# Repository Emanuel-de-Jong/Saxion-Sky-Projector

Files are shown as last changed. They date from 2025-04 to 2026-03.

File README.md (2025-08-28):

# Sky Projector
For the class: 3.3 CDT Increadible machines

A DIY controllable and customizable 3-in-1 sky projector. The code is nothing special, but the technical components, prototyping and planning were interesting. I made a schematic and a 3d model and used components like MOSFETs and PWM Drivers.

With the high power LEDS, I also had to take heat into account in multiple places. Aluminium bases, a fan and even a thick heatsink were needed.

**Active Development:** 2025-03-17 - 2025-04-21<br>
**Last Change:** 2025-05-08<br>

| | |
| :---: | :---: |
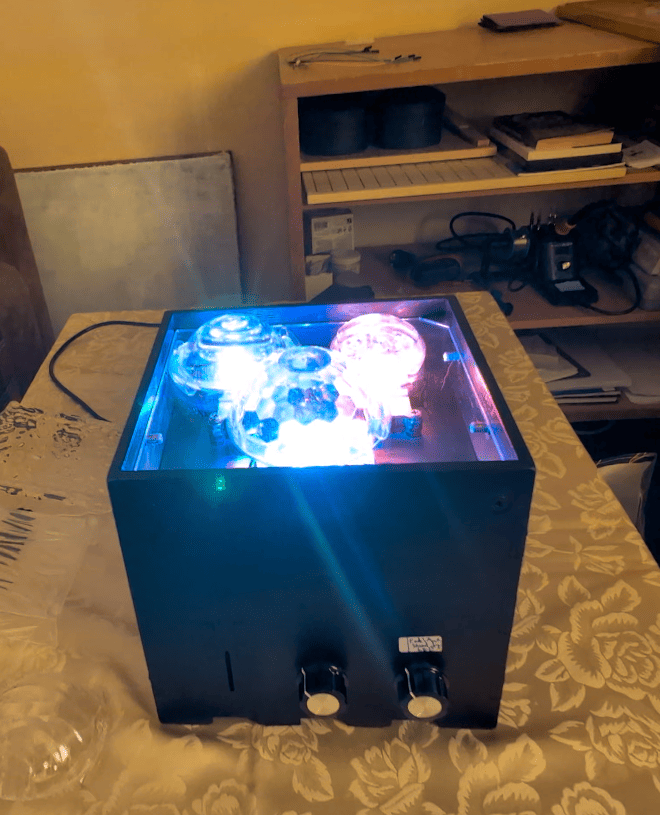
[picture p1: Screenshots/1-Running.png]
|  |  |
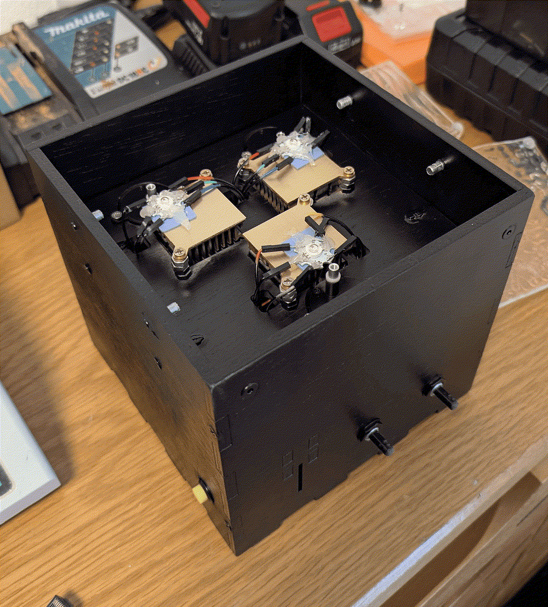
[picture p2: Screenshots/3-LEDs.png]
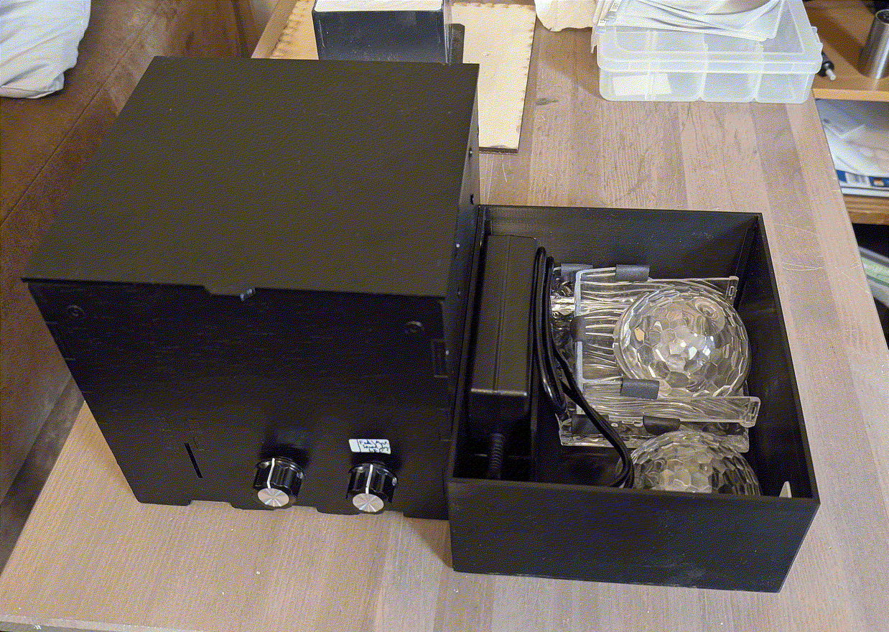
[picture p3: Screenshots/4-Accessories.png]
|  |  |
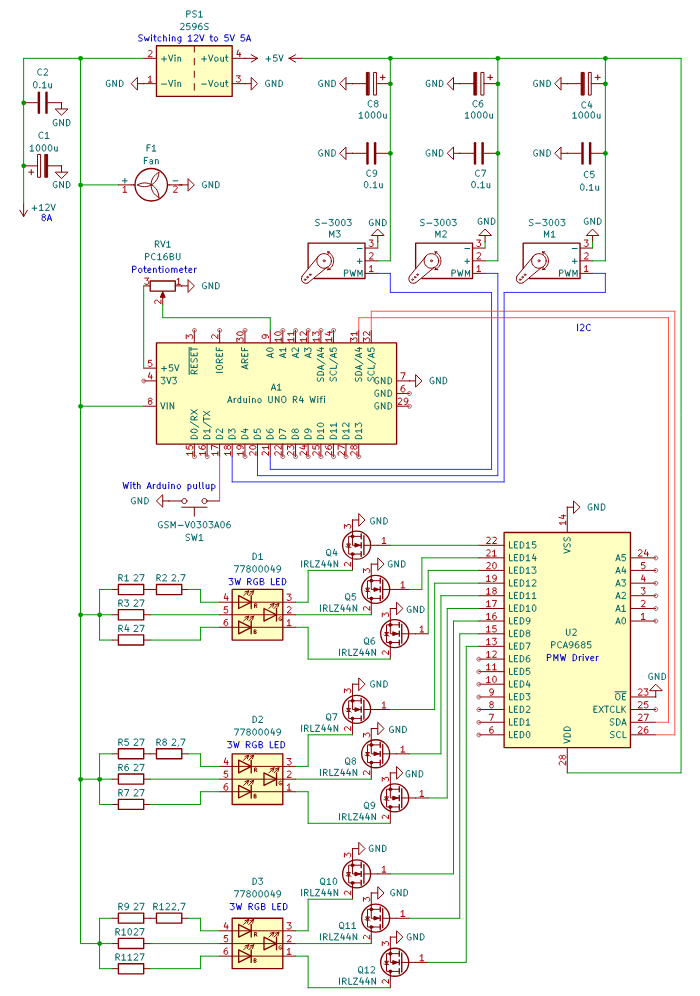
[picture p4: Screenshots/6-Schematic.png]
|  |  |
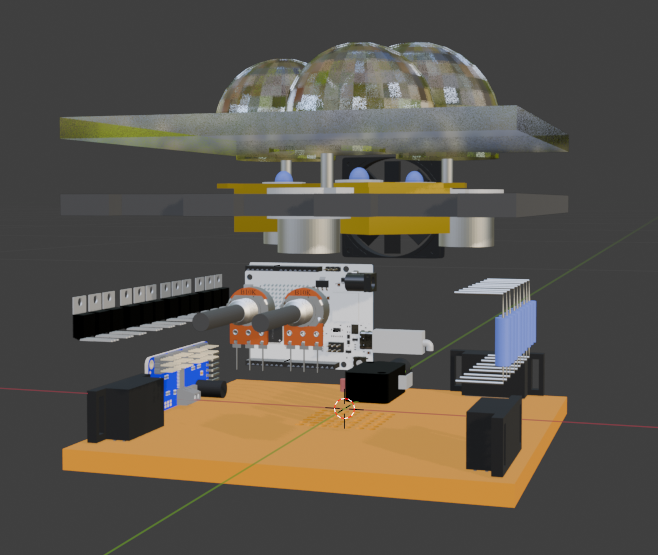
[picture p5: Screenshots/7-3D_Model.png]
|  |  |

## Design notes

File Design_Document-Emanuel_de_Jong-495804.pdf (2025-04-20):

# Incredible Machines

## Design Document (2024-2025)

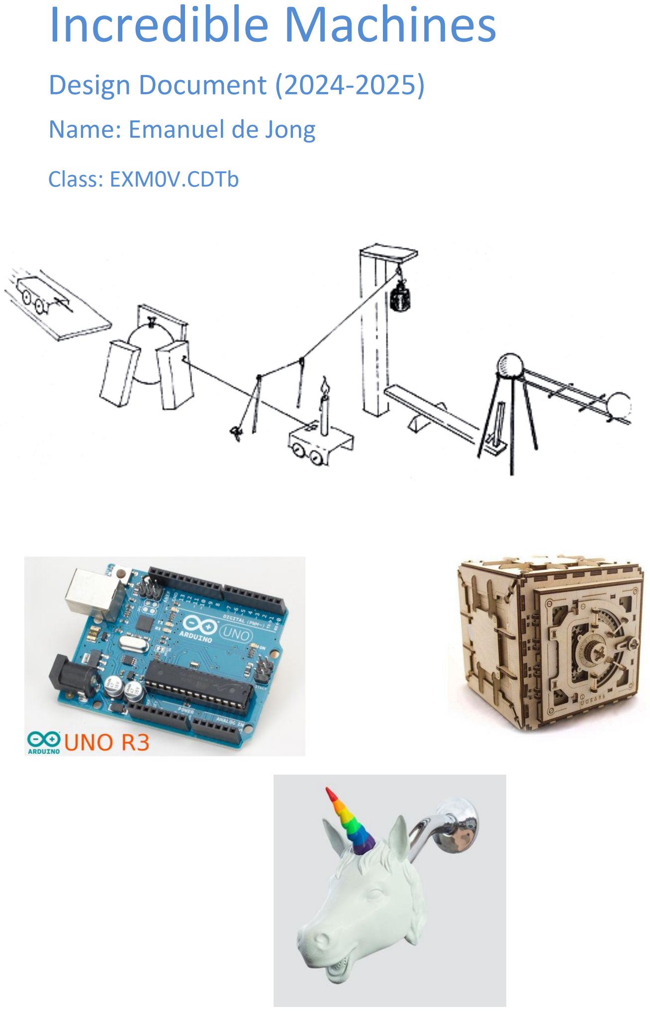
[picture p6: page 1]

## Name: Emanuel de Jong

## Class: EXM0V.CDTb

Incredible Machines | page 2

Content:

1 | Concept descriptions | 3
1.1 | Concepts | 3
1.2 | Your Incredible Machine | 5
2 | Morphological Chart | 7
3 | Sensors and Actuators | 8
Reasons for selection: | 9
4 | Tests of (small) prototypes (proof of concept) | 9
5 | Connection schematics | 17
6 | 3D printing and laser cutting | 18
7 | Used software | 18
Code snippets | 18
8 | Final result | 20
9 | Reflection | 20

### 1 Concept descriptions

### 1.1 Concepts

Concept A: Aurora projector
A mostly round box with a patterned glass dome or plate on top. A red, green and blue light with a motor for each turning them up to 120 degrees horizontally to create a changing light pattern on any ceiling and partly wall. Putting a card in a card slot starts the machine. There is also a knob to change the speed of the motors.

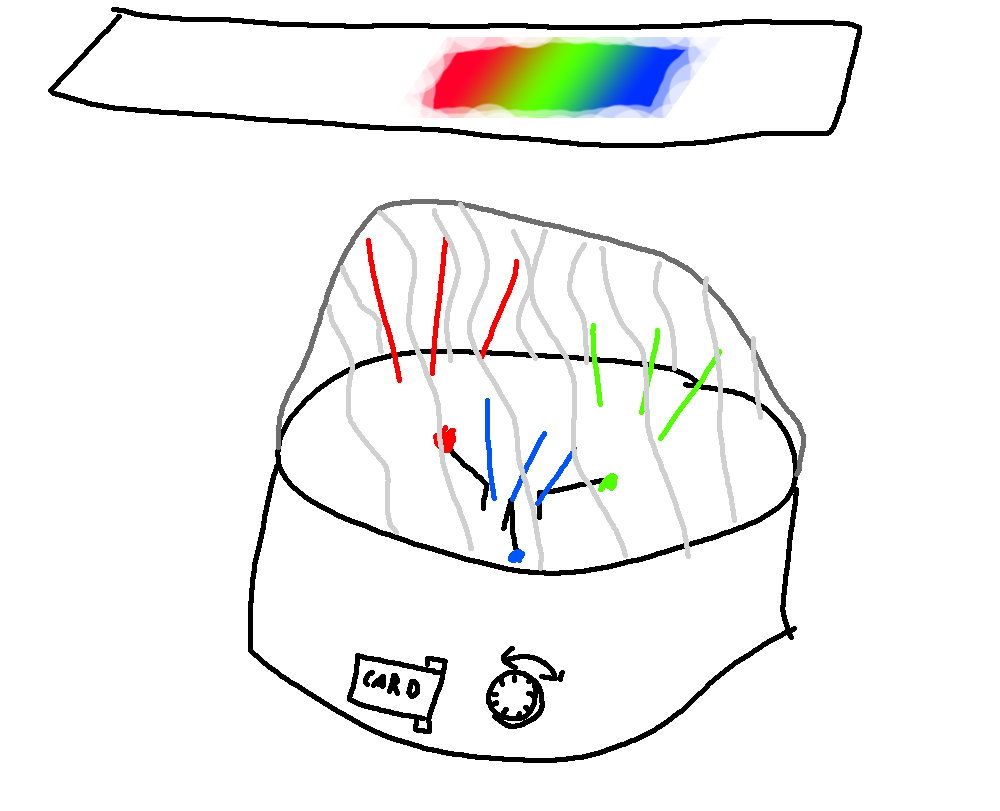
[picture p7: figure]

Concept B: Escape box
A rectangular box with challenges. Turning a key in a keyhole turns on the game. Three lights that start turned on indicate lives. When you fail the challenge you lose a live. When you lose all lives you failed the game. When you solved all challenges you win the game. A sound indicates when you won or lost depending on the sound.

The first challenge is Simon says with 3 colour buttons with lights in them. It starts with 1 light increasing the sequence by 1 up to a sequence of 5.

The second challenge is a meter turning left and right quickly. When pressing a button, the meter stops, if it stops in a certain range, you passed. The range is indicated by a colour strip.

The third challenge is writing a 4 digit code from morse deeps that start after finishing the first challenge. The morse codes for digits is in the manual. When 4 digits are given and it’s wrong, you lose a life and the digit display clears.

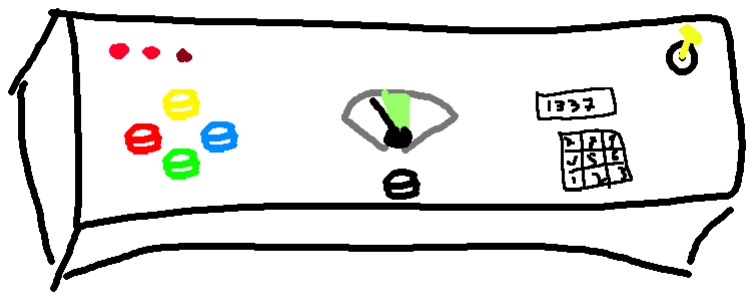
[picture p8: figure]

Concept C: Portable fan
A small fan for hot summers. Can be folded to bring with you. Turns on by blowing into a hole. With a button you can toggle between 3 speed settings. 3 lights indicate which speed it’s on.

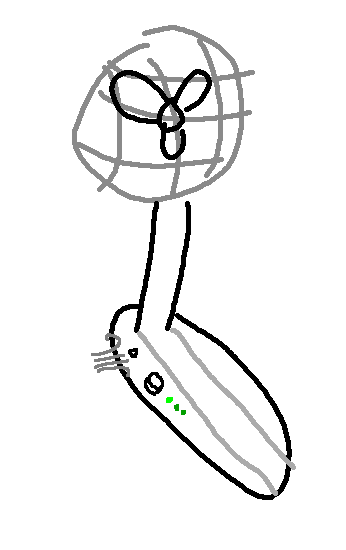
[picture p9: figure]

Conclusion
I chose concept A because I’m most interested in it and it’s the only concept I will use after the project. It’s also simple enough to be manageable in the time of the project, at least I thought so.

### 1.2 Your Incredible Machine

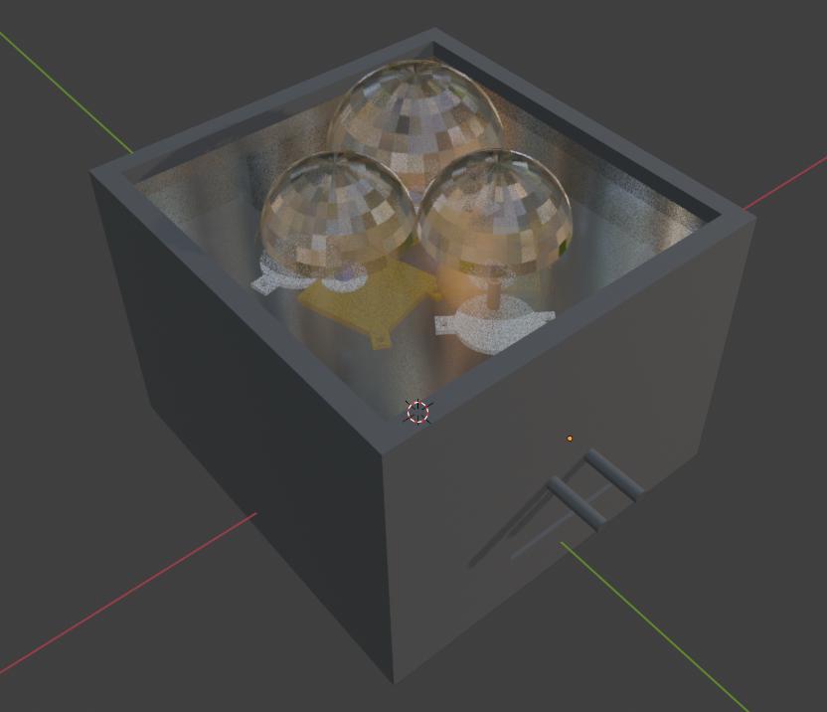
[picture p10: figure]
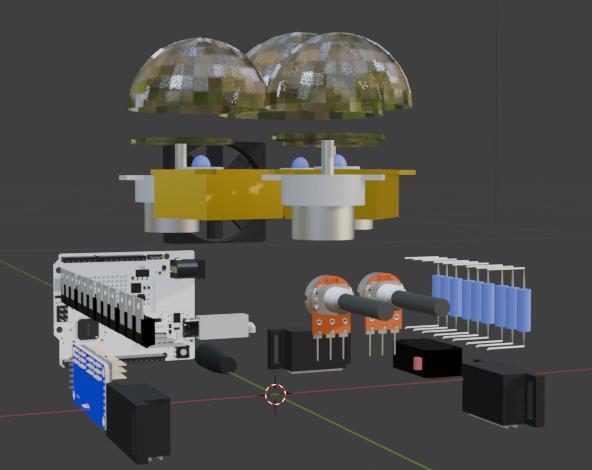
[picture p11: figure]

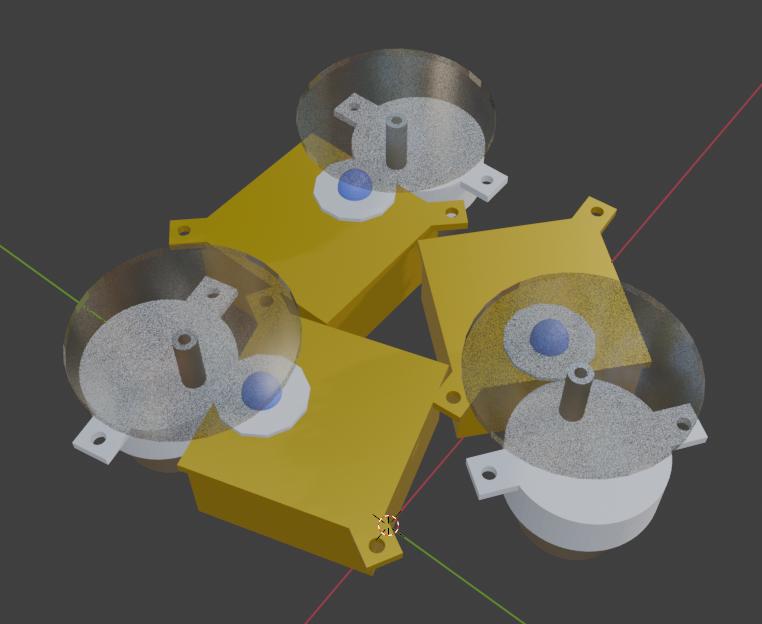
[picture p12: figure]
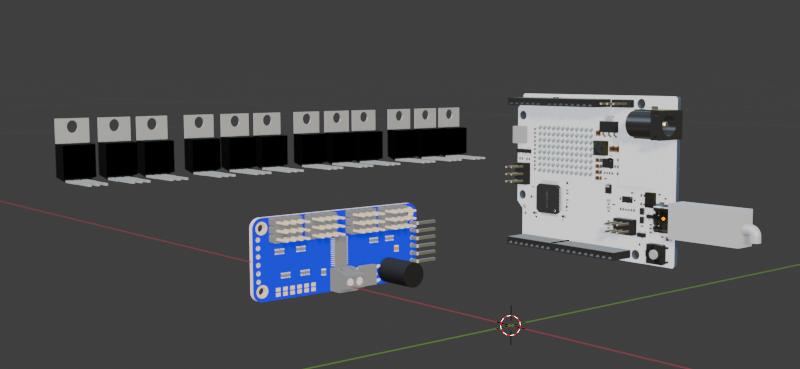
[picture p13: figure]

Because a rectangular shape for the box is more practical, e.g. to fasten it to the wall, I choose not to use a cylindrical shape. The outside vertical walls will be black 3d printed plastic. The bottom is wood with a hole big enough for any finger to open it up for maintenance. The Arduino is held in a small plastic container screwed to the side. Above the Arduino there is a 3D printed plate for the LED’s and the rotating lenses. It has a hole in the centre for the cables. The glass domes, not only one, but I choose to use three of them for advanced effects, rests on a transparent horizontal plate as a third level on which the different secondary lenses can be put. As a fourth and final level there is a transparent plate on top of the box.

### 2 Morphological Chart

Materials
Goal | Option 1 | Option 2 | Option 3 | Reason
Lens | Glass | Plexiglass | Polycarbonate | Only patterned lenses from other sky projectors are good enough as they are made for caustics. The sky projectors I have use polycarbonate lenses.
Casing | Wood | PLA | Metal | As I’d like to use the product after the project, I would like a professional look. Wood feels too DIY. Metal is professional but is hard to work with. With PLA I can easily 3d print it.
Bottom | Wood | PLA | Metal | A thin circular plate is easy to make with normal cutting. Wood has the benefit of being cheap and adaptable for fixing things on it, also it is easy to alter the concept.

Hardware and software
Goal | Option 1 | Option 2 | Option 3 | Reason
Microcontroller | Arduino | ESP | Raspberry Pi | The casing is big enough to fit an Arduino and the tasks are simple enough so that a raspberry would be overkill. It’s also what I already have and am used to.
Language | Arduino programming language | Visual | Maschinecode | Gives more freedom and complexity is not a problem for me as software

| | | | engineering is my major.
IDE | Arduino IDE 1 | Arduino IDE 2 | VS Code | I’ve had bad experiences with both versions of the official IDE. VS Code can do everything they can and more.

### 3 Sensors and Actuators

Sensors
Goal | Option 1 | Option 2 | Option 3 | Option 4
Card detection | Microswitch | IR proximity sensor | Ultrasonic module | Laser interruption module
First lens Rotation | DC motor | Stepper motor | Servo motor
Light rotation speed control + Colour changing speed | Slider | Potentiometer | Button (toggle values)
Light | Standard LED | RGB LED | Halogen lamp | Light bulb

Reasons for selection:

Card detection
While an IR sensor is a logical and viable option, nothing beats the reliability and ease of a microswitch being pressed down by the side of the card. It also doesn’t suffer from environmental issues like light or sound which are both present inside the product.

First lens rotation
The stepper motor is expensive and needs a driver module , we don’t need it’s strength either. Cheap versions are also jittery making the light effect less satisfying. The servo motor I received had only a quarter radius forward and back modus, while I need a continuous circular movement. A DC motor is perfect for this and its speed is easily regulated by a potentiometer.

Light rotation speed control + Colour changing speed
A button would be restrictive as it jumps between values. It’s also more tedious to go from a middle state to the lowest state having to press multiple times. Although a slider would work, a potentiometer is the more usual regulator in commercial products.

Light
An RGB LED gives more creative freedom for cool effects so I’ll choose it. However, single colour LEDs can get brighter without outside power than RGB LEDs . unfortunately You would need more space for them and the light source would be less concentrated on one point, so the projection could be less fluent.

### 4 Tests of (small) prototypes (proof of concept)

Of course there a many stages, so I only describe the main stages here. The reason to move to a next stage is mostly extension to the final product. Changes and their reason are written between the lines.

Preparation
Many, many components

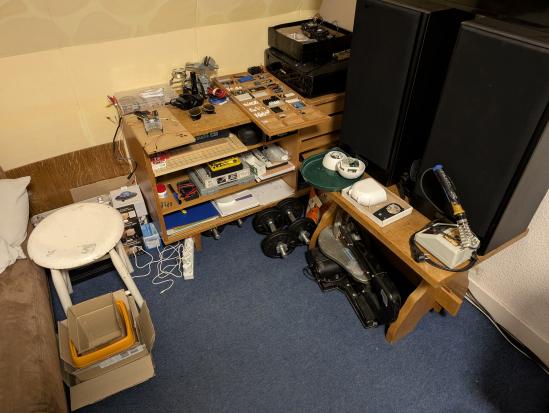
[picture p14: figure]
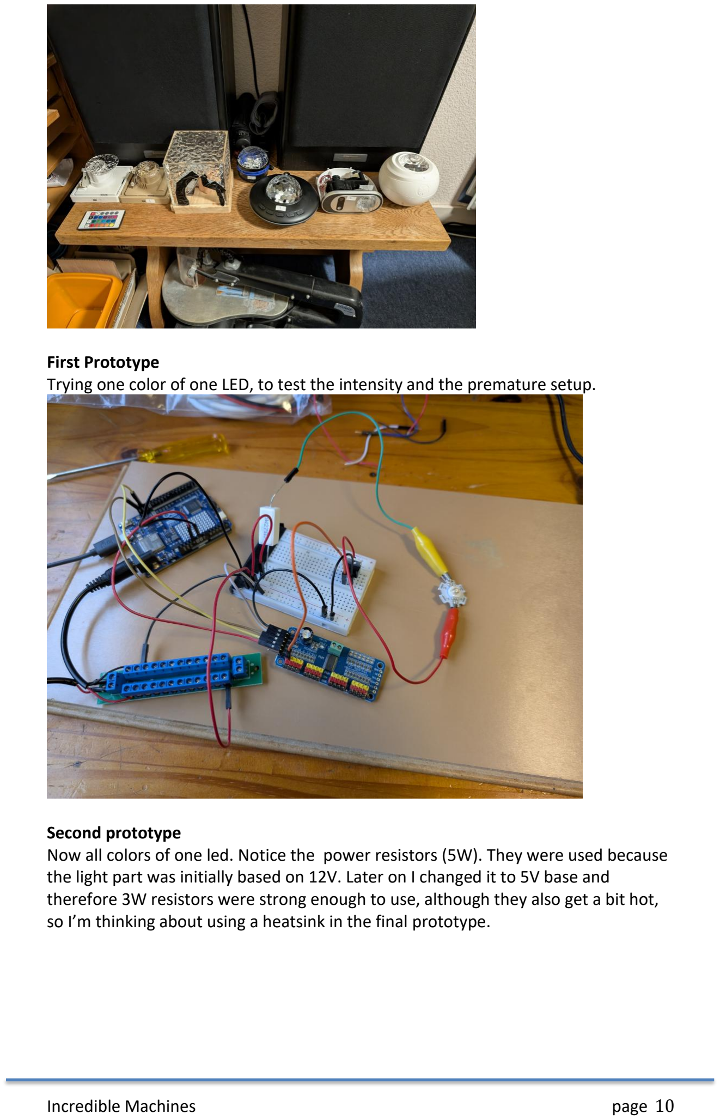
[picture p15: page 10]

First Prototype
Trying one color of one LED, to test the intensity and the premature setup.

Second prototype
Now all colors of one led. Notice the power resistors (5W). They were used because the light part was initially based on 12V. Later on I changed it to 5V base and therefore 3W resistors were strong enough to use, although they also get a bit hot, so I’m thinking about using a heatsink in the final prototype.

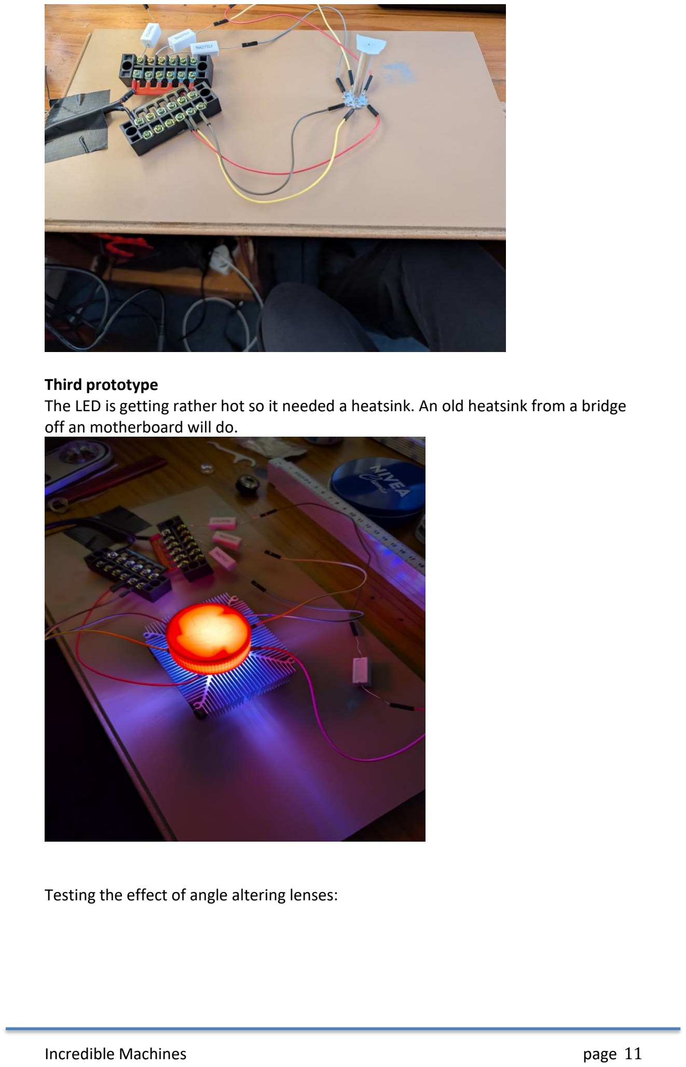
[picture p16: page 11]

Third prototype
The LED is getting rather hot so it needed a heatsink. An old heatsink from a bridge off an motherboard will do.

Testing the effect of angle altering lenses:

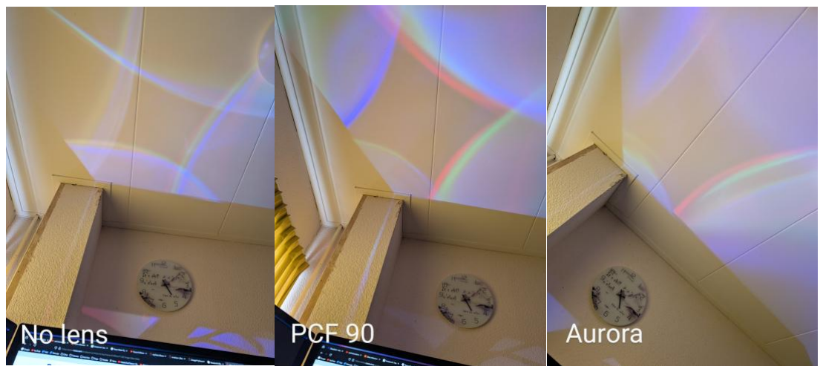
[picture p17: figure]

Fourth prototype
Now the Arduino is basically programmed and connected.
This and the next prototypes have no pictures as they went fast due to the experiences I gained from the previous ones.

Fifth prototype
Now rotation comes into play and I connect the dc-motors to irregular lenses that are to be rotated above the individual LEDS’s. For regulating their speed I need an RPM module, because the rpm possibilities on the Arduino are less then I need. Additional there are MOSFETs needed to let the whole thing function.

Sixth prototype
Introducing the light effects is the next stage. There are also MOSFETs and (of course other parts of) the rpm driver needed.

Seventh prototype
Now the combination from in different speed rotating lenses and the speed of light change in combination with colour change is the item. This is a really long path to find the right combinations.

Eight prototype
The experiments with secondary lenses start. The setup is now fully crowdy and it is a lot of fun the experience the possibilities.

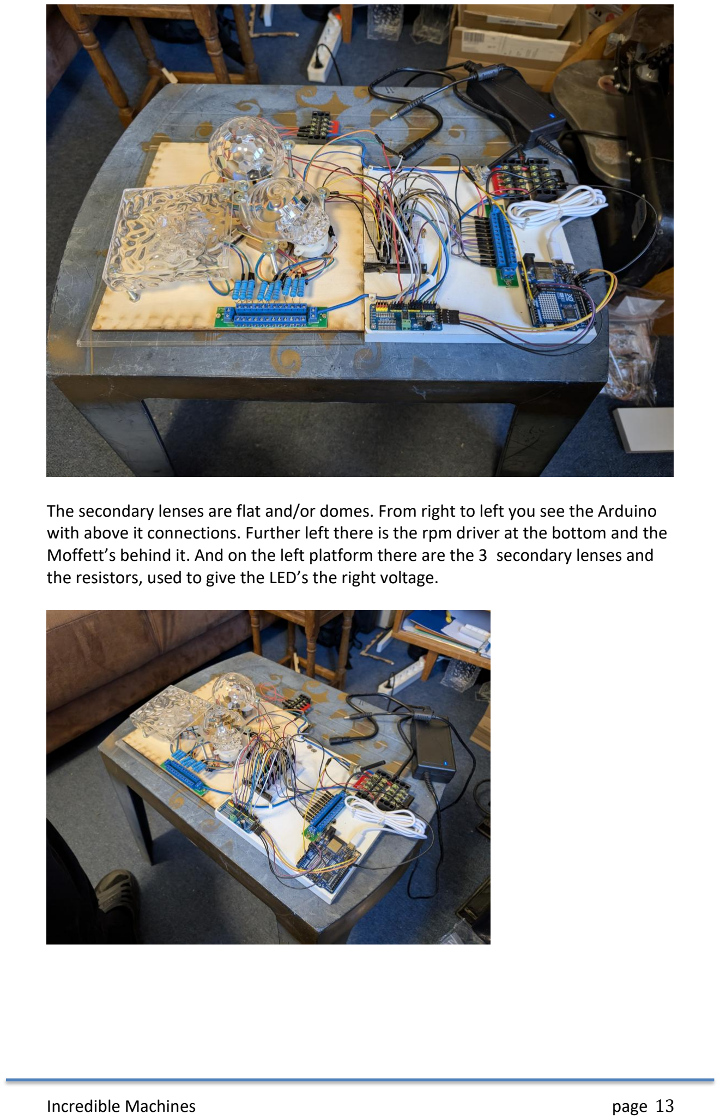
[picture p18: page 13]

The secondary lenses are flat and/or domes. From right to left you see the Arduino with above it connections. Further left there is the rpm driver at the bottom and the Moffett’s behind it. And on the left platform there are the 3 secondary lenses and the resistors, used to give the LED’s the right voltage.

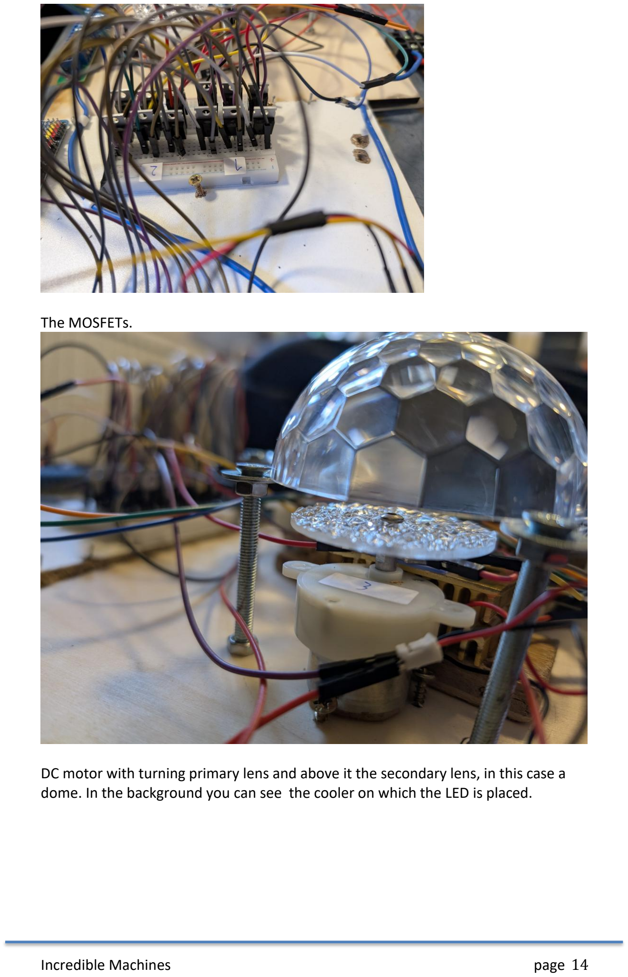
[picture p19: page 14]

The MOSFETs.

DC motor with turning primary lens and above it the secondary lens, in this case a dome. In the background you can see the cooler on which the LED is placed.

3 directional lenses

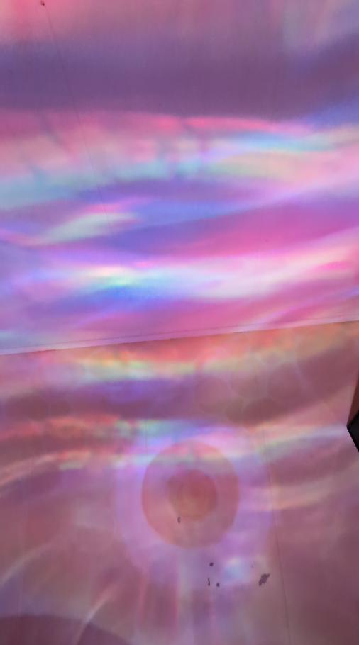
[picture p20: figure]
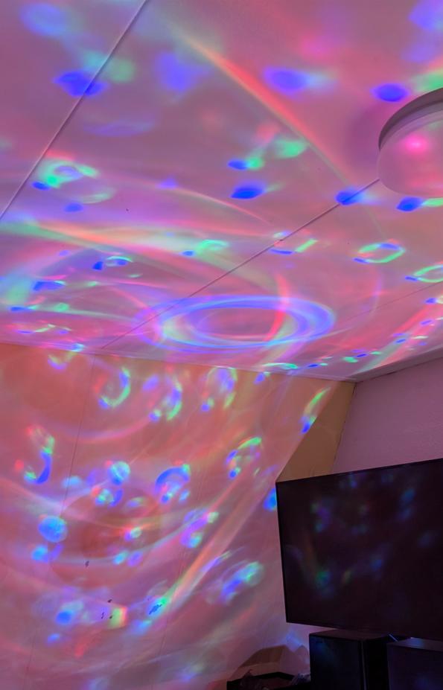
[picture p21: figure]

3 global/circular lenses

A shared lens

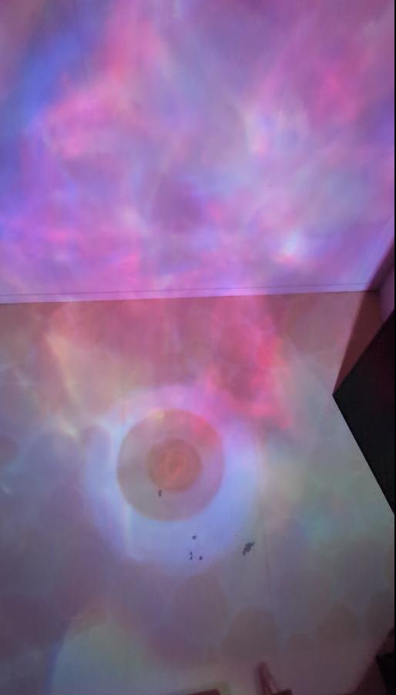
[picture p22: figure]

Only the disc lenses for light distribution

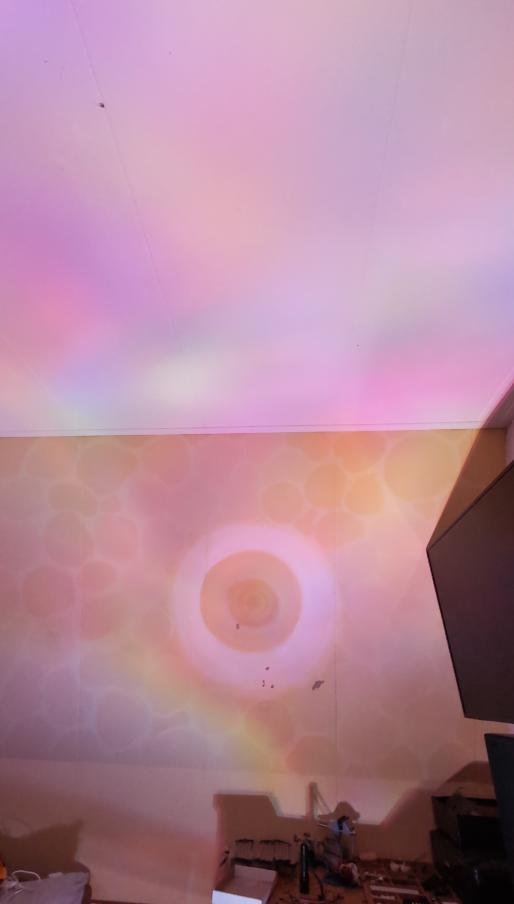
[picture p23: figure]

Way to final product

The whole construction is to be made fit into a 3Dprinted box with wooden bottom on which the electronics should find their place. Then a second layer in it with LED’s, motors and primary lenses. Above that a transparent plate on which the diverse secondary lenses will be placed. And finally on top another transparent plate. This part is still to be finally built.

### 5 Connection schematics

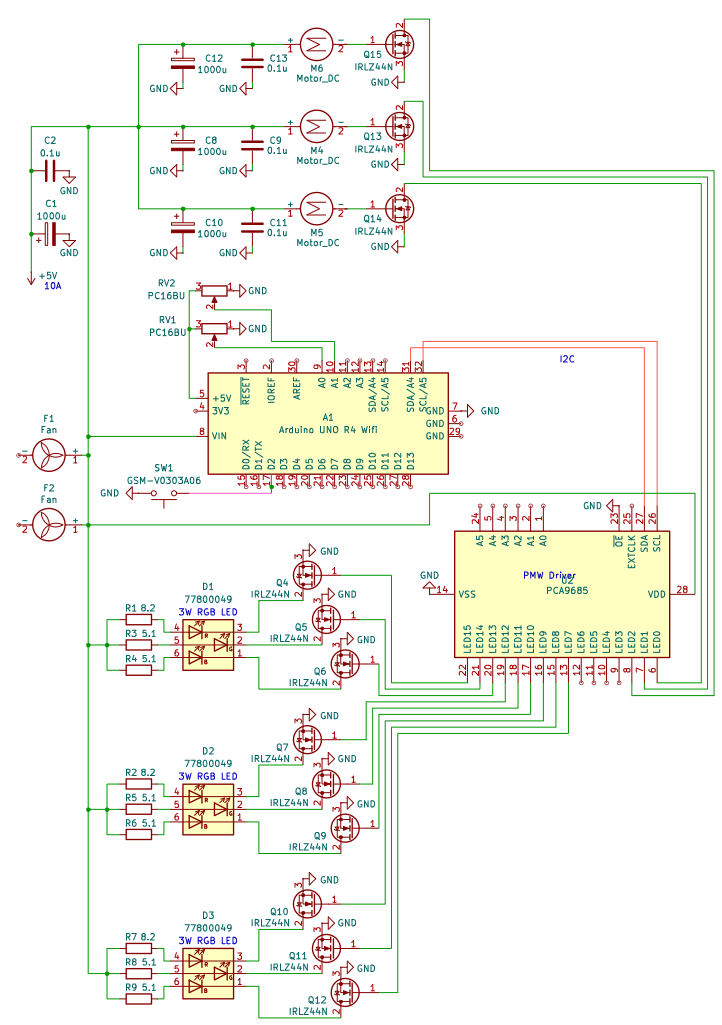
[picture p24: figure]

The projector is powered by a 5V 10A power adapter, though A 6A one should suffice.

The electrolytic and ceramic capacitors are for stability and filtering high frequency noise. There is a pair at the entrance and at each motor as you don’t want trailing motors and they can stall which might draw a high amount of current for a short period.
The ground pin of each motor goes to it’s own MOSFET and connects to its drain. The MOSFETs source is connected to ground and the gate goes to a pin on the PWM driver so the Arduino can alter the motors speed.

Each colour channel of each RGB LED works in the same way with the addition of a 3W resistor (8.2 ohm for red and 5.1 for green/blue) to lower the voltage.

The Arduino has 2 potmeters connected like usual. The microswitch uses the Arduino’s built in pullup for noise reduction. The Arduino connects to the PWM driver using I2C. The Arduino’s ground is connected to common ground to equalize for safety.

Lastly there are 2 fans. One blows air through the whole projector, the other is directed to the resistors as they generate a high amount of heat.

6 3D printing and laser cutting

The walls of the box and the floor separating the main electronics and the LEDS/motors/lenses are 3D printed.
The two transparent plates and the top are laser cut.

### 7 Used software

I used the Arduino programming language, because the microprocessor used is an Arduino. The software does its work as expected.

Each colour of each LED fades at different speeds. Each DC motor has its own speed. The microswitch to turn the product on and the potmeters for the movement speed and fade speed are still to be added.

Code snippets

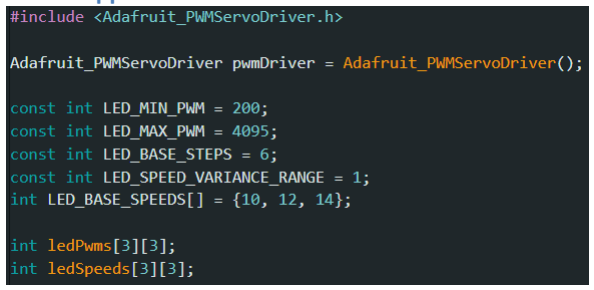
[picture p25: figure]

I used a library to easily control the PWM driver without having to worry about I2C connections and such. All I have to do is use the functions of pwmDriver.

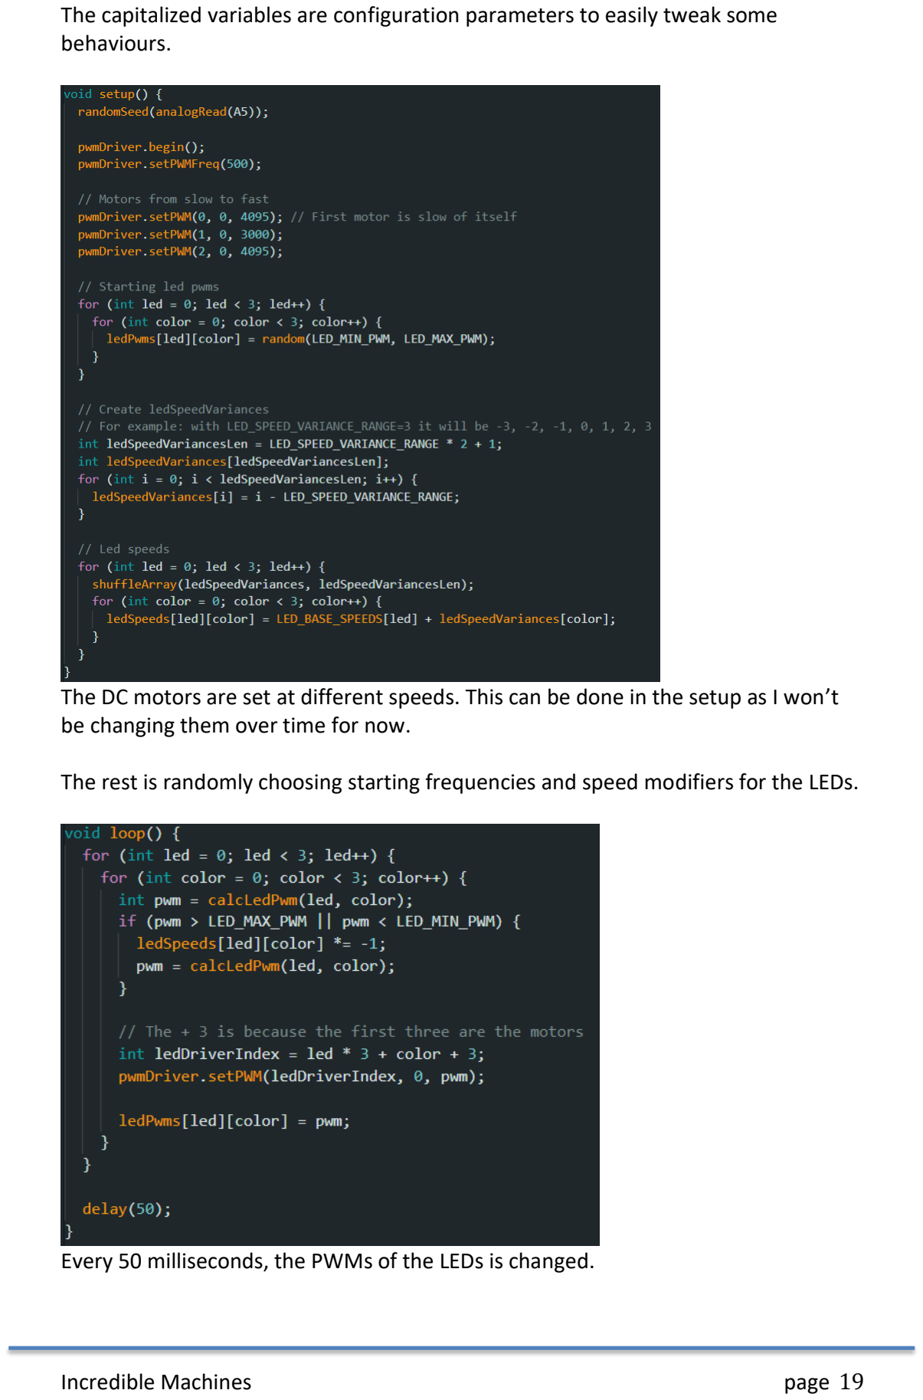
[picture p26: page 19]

The capitalized variables are configuration parameters to easily tweak some behaviours.

The DC motors are set at different speeds. This can be done in the setup as I won’t be changing them over time for now.

The rest is randomly choosing starting frequencies and speed modifiers for the LEDs.

Every 50 milliseconds, the PWMs of the LEDs is changed.

### 8 Final result

As mentioned earlier, the final build is still being worked on.

### 9 Reflection

The Arduino Shield was not useful for this setup, so nothing to tell about that. The microswitch I used is a very simple example of a place/situation sensor. The potentiometer is a useful sensor for setting your preferences to influence the outcome of the effects.

During the programming I was confronted for the first time with a PWM driver. That this PWM module is also useful for the light part was a surprise for me.

I learned a lot about resistors and how to calculate current and voltages so the LED becomes the right Voltage. I also learned this creates a lot of heat.

Further on I was studying the world of relays, switches, transistors and MOSFETs, quite a bit of electronics for a software student!

The soldering of the LEDs, the wiring of the MOSFETs and getting the lenses from other projectors took a lot longer than I anticipated. This made it hard since I needed a fully working prototype to test out effect so that I could decide on one, so that I could think of how the final product will look so that I could finish this document… In future products I think I will choose something with less connections.

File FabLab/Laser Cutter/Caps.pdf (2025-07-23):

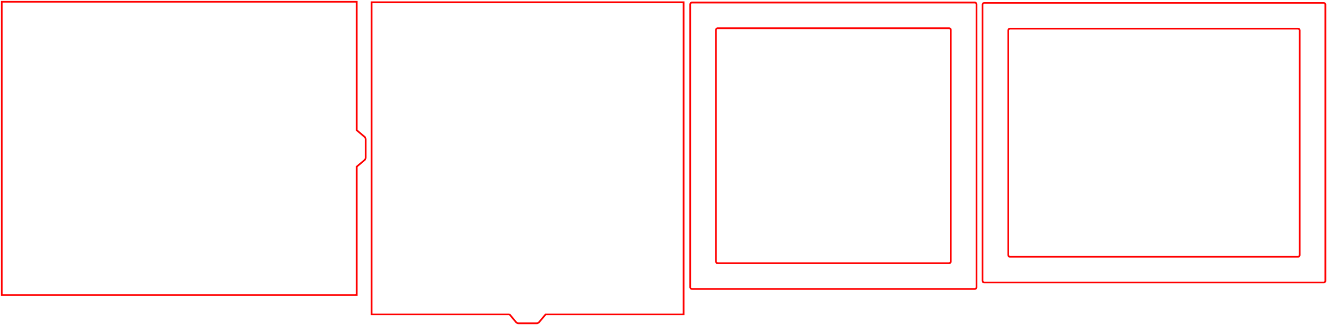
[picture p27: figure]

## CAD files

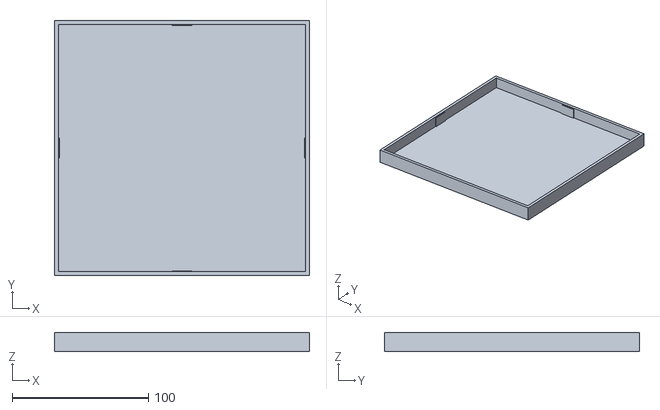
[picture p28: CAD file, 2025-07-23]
FabLab/3D Printer/Projector Cap.stl
187.0 x 187.0 x 14.0

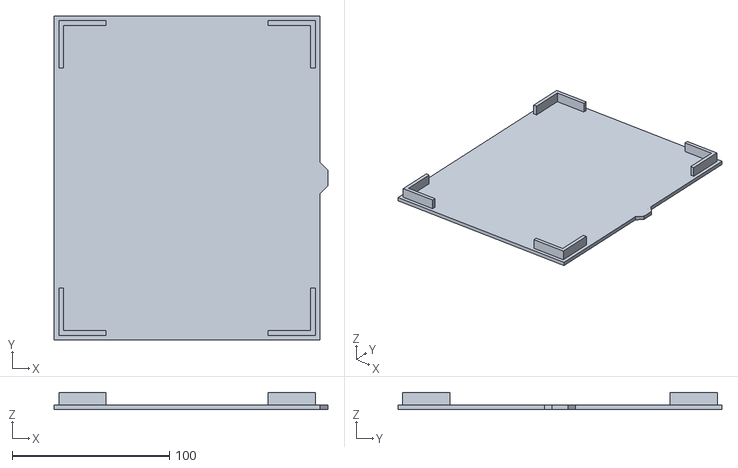
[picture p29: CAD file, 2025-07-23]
FabLab/3D Printer/Lens holder cap.stl
174.0 x 206.0 x 11.0

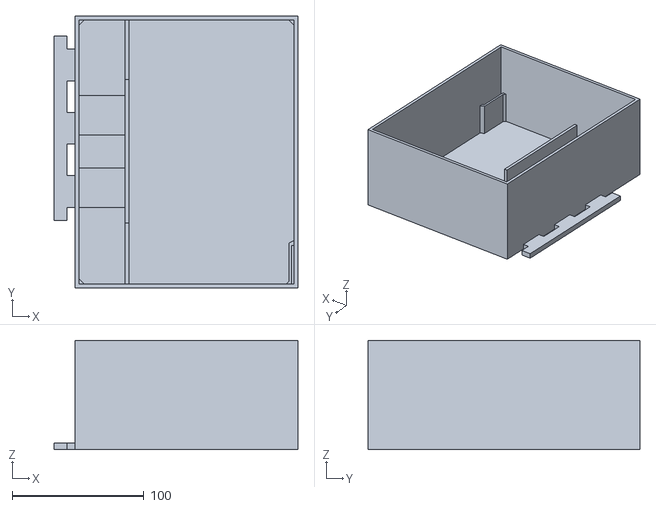
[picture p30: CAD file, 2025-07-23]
FabLab/3D Printer/Lens holder.stl
185.0 x 206.0 x 83.0

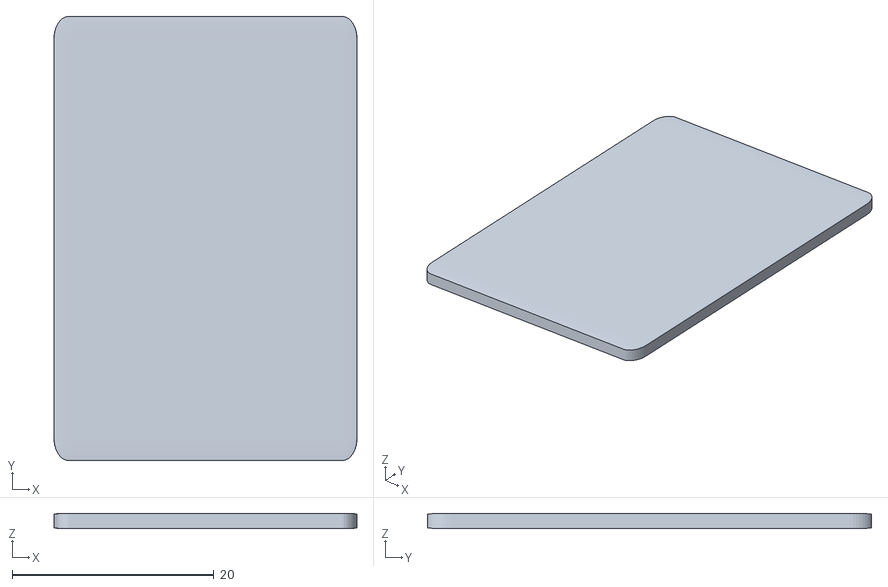
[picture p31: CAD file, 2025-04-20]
FabLab/3D Printer/Creditcard.stl
30.0 x 44.0 x 1.50

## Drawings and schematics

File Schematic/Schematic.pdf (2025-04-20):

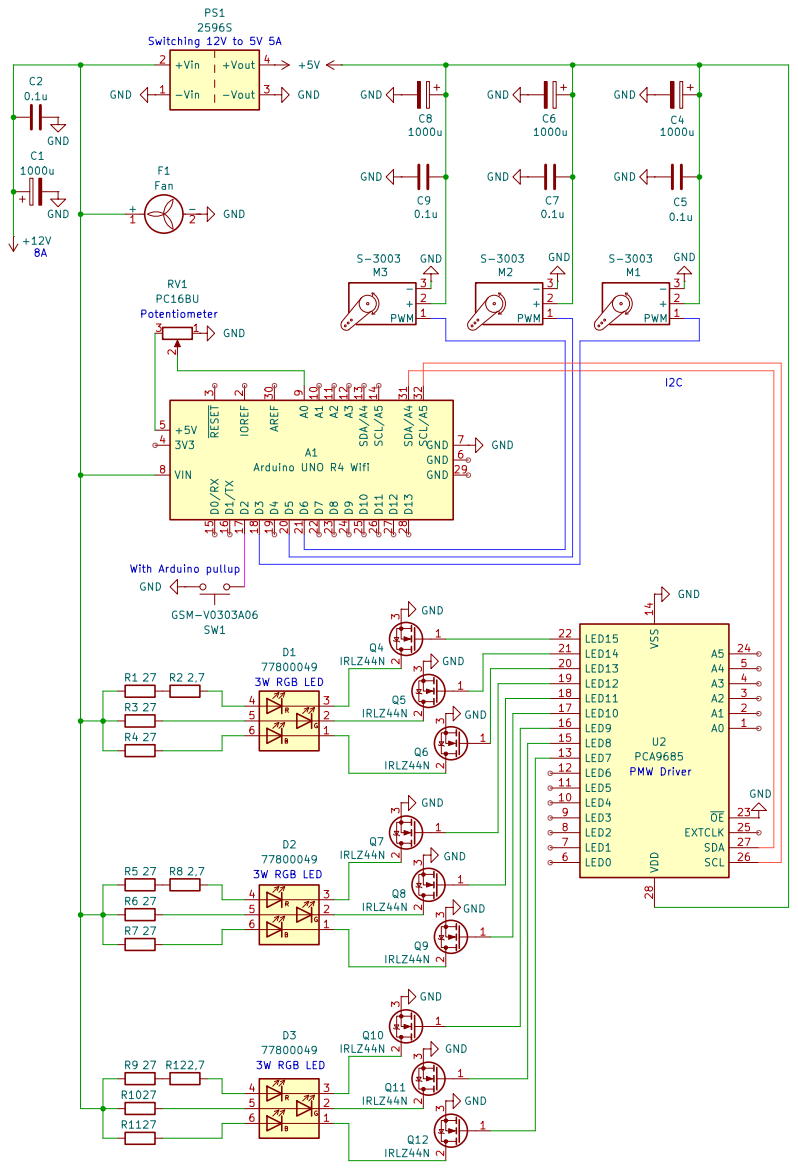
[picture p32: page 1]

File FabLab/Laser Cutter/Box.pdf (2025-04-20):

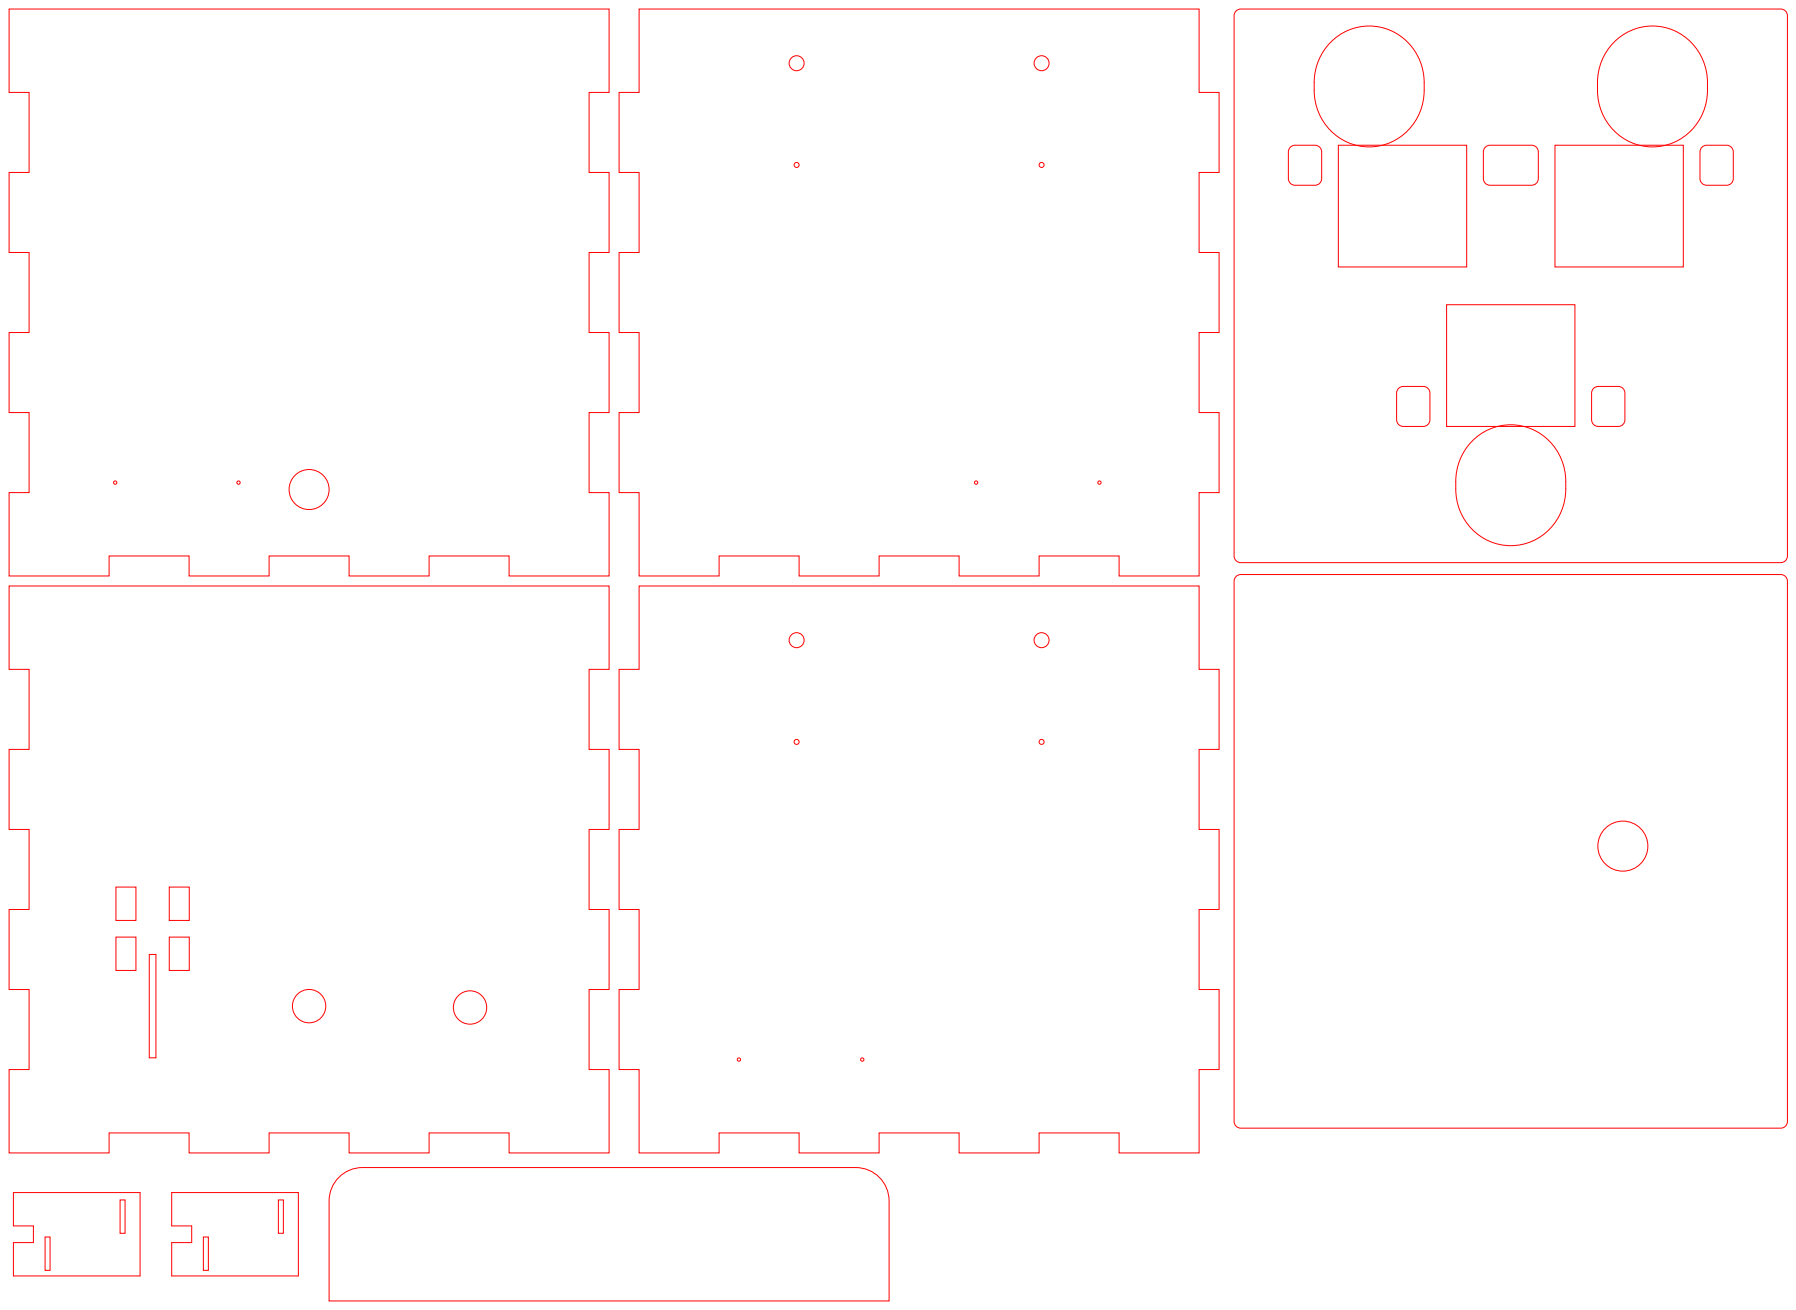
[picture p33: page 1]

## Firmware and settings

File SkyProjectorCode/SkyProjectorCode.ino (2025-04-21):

#include <Adafruit_PWMServoDriver.h>

Adafruit_PWMServoDriver pwmDriver = Adafruit_PWMServoDriver();

// LEDS
// PIN 0-2 = no label
// PIN 3-5 = label three
// PIN 6-8 = label six

// MOTORS
// PIN 9 = label three
// PIN 10 = label six
// PIN 11 = no label

const int POT_MAX = 1023;
const int PWM_MAX = 4095;

const int SWITCH_PIN = 12;
const int BTN_PIN = 11;
const int LED_POT_PIN = A1;
const int MOTOR_POT_PIN = A0;

const int TIME_BEFORE_SWITCH_REGISTER = 200;

bool isOn = false;
unsigned long switchTime = 0;

const unsigned long BTN_VALIDATION_COUNT_THRESHOLD = 3;
const unsigned long BTN_SHORT_THRESHOLD = 500;
const int COLOR_MODE_COUNT = 9;
const int COLOR_SCOPE_COUNT = 2;
const bool COLOR_MODES[9][9] = {
  {1,1,1, 1,1,1, 1,1,1}, // rgb
  {1,0,0, 1,0,0, 1,0,0}, // r
  {0,1,0, 0,1,0, 0,1,0}, // g
  {0,0,1, 0,0,1, 0,0,1}, // b
  {1,1,0, 1,1,0, 1,1,0}, // rg
  {1,0,1, 1,0,1, 1,0,1}, // rb
  {0,1,1, 0,1,1, 0,1,1}, // gb
  {1,0,0, 0,1,0, 0,0,1}, // r, g, b
  {1,1,0, 1,0,1, 0,1,1} // rg, rb, gb
};

unsigned long btnTime = 0;
int btnValidationCount = 0;
bool isColorModeChanged = true;
int colorMode = 0;
// 0=Per color, 1=Per led
int colorScope = 0;

const int SPEED_MOD_MIN = 1;
const int SPEED_MOD_MAX = 100;

const int LED_MIN_PWM = 200;
const int LED_BASE_STEPS = 15;
const float LED_SPEED_MIN = 0.7;
const float LED_SPEED_MAX = 1.3;
const int LED_SPEED_CHANGE_TIME_MIN = 1000;
const int LED_SPEED_CHANGE_TIME_MAX = 5000;
const float LED_FADE_DEPTH_SPEEDS[] = {1.3, 1.0, 0.7};
const int LED_TOGGLE_TIME_MIN = 75;
const int LED_TOGGLE_TIME_MAX = 2000;

// 0=Static, 1=Fade, 2=Toggle
int ledMode = 0;
float ledSpeedMod = 1;
int ledPwms[3][3];
int ledDirections[3][3];
float ledSpeeds[3][3];
int ledSpeedTimesBeforeChange[3][3];
unsigned long ledSpeedChangeTimes[3][3];
unsigned long lastColorChange = millis();
bool lastColorCombination[9] = {};

const int MOTOR_MIN_PWM = 600;
const float MOTOR_DEPTH_SPEEDS[] = {1.0, 0.8, 0.9};

// 0=Off, 1=Global, 2=Depth
int motorMode = 0;
float motorSpeedMod = 1;

void setup() {
  randomSeed(analogRead(A5));
  Serial.begin(9600);

  pinMode(SWITCH_PIN, INPUT_PULLUP);
  pinMode(BTN_PIN, INPUT_PULLUP);

  pwmDriver.begin();
  pwmDriver.setPWMFreq(100);

  // Led fade init
  for (int led = 0; led < 3; led++) {
    for (int color = 0; color < 3; color++) {
      ledDirections[led][color] = random(2) == 1 ? 1 : -1;
      ledSpeeds[led][color] = randomFloat(LED_SPEED_MIN, LED_SPEED_MAX+1);
      ledSpeedTimesBeforeChange[led][color] = random(LED_SPEED_CHANGE_TIME_MIN, LED_SPEED_CHANGE_TIME_MAX+1);
      ledSpeedChangeTimes[led][color] = millis();
    }
  }
}

float randomFloat(float min, float max) {
  float resolution = 100.0;
  int min_int = min * resolution;
  int max_int = max * resolution;
  return random(min_int, max_int + 1) / resolution;
}

void loop() {
  if (!checkIsOn()) {
    return;
  }

  checkMode();
  checkLedPot();
  checkMotorPot();

  loopLeds();
  loopMotors();

  isColorModeChanged = false;

  delay(25);
}

bool checkIsOn() {
  bool isSwitchPressed = digitalRead(SWITCH_PIN) == LOW;
  if (!isSwitchPressed && !isOn || isSwitchPressed && isOn) {
    if (switchTime == 0) {
      switchTime = millis();
    } else if (millis() - switchTime >= TIME_BEFORE_SWITCH_REGISTER) {
      switchTime = 0;
      if (isOn) {
        turnOff();
      } else {
        turnOn();
      }
    }
  }

  return isOn;
}

void turnOn() {
  isOn = true;
}

void turnOff() {
  clearLeds();
  clearMotors();

  isOn = false;
}

void clearLeds() {
  for (int color = 0; color < 9; color++) {
    pwmDriver.setPWM(color, 0, 0);
  }
}

void clearMotors() {
  for (int motor = 9; motor < 12; motor++) {
    pwmDriver.setPWM(motor, 0, 0);
  }
}

void checkMode() {
  bool isBtnPressed = digitalRead(BTN_PIN) == LOW;

  if (isBtnPressed) {
    btnValidationCount++;
  }

  if (isBtnPressed && btnTime == 0) {
    btnTime = millis();
  } else if (!isBtnPressed && btnTime != 0) {
    if (btnValidationCount >= 3) {
      unsigned long btnDuration = millis() - btnTime;
      if (btnDuration <= BTN_SHORT_THRESHOLD) {
        colorMode++;
        if (colorMode == COLOR_MODE_COUNT) {
          colorMode = 0;
        }

        isColorModeChanged = true;
      } else {
        colorScope++;
        if (colorScope == COLOR_SCOPE_COUNT) {
          colorScope = 0;
        }
      }
    }

    btnTime = 0;
    btnValidationCount = 0;
  }
}

void checkLedPot() {
  int ledPotVal = analogRead(LED_POT_PIN);
  int rangeStart = 0;
  int rangeEnd = 0;
  if (ledPotVal == 0) {
    ledMode = 0;
  } else if (ledPotVal >= 1 && ledPotVal <= 500) {
    ledMode = 1;
    rangeStart = 1;
    rangeEnd = 500;
  } else if (ledPotVal >= 501 && ledPotVal <= POT_MAX) {
    ledMode = 2;
    rangeStart = 501;
    rangeEnd = POT_MAX;
  }

  ledSpeedMod = calcSpeedMod(ledPotVal, rangeStart, rangeEnd);
}

float calcSpeedMod(int potVal, int rangeStart, int rangeEnd) {
  float resolution = 100.0;
  float upperCapPerc = 0.12;
  float upperCap = rangeEnd - (rangeEnd - rangeStart) * upperCapPerc;

  if (potVal >= upperCap) {
    return SPEED_MOD_MAX;
  }

  return map(potVal, rangeStart, upperCap, SPEED_MOD_MIN, SPEED_MOD_MAX * resolution) / resolution;
}

void checkMotorPot() {
  int motorPotVal = POT_MAX - analogRead(MOTOR_POT_PIN);
  int rangeStart = 0;
  int rangeEnd = 0;
  if (motorPotVal == 0) {
    motorMode = 0;
  } else if (motorPotVal >= 1 && motorPotVal <= 500) {
    motorMode = 1;
    rangeStart = 1;
    rangeEnd = 500;
  } else if (motorPotVal >= 501 && motorPotVal <= POT_MAX) {
    motorMode = 2;
    rangeStart = 501;
    rangeEnd = POT_MAX;
  }

  motorSpeedMod = calcSpeedMod(motorPotVal, rangeStart, rangeEnd);
}

void loopLeds() {
  if (ledMode == 0) {
    for (int color = 0; color < 9; color++) {
      if (COLOR_MODES[colorMode][color]) {
        pwmDriver.setPWM(color, 0, PWM_MAX);
      } else {
        pwmDriver.setPWM(color, 0, 0);
      }
    }
  } else if (ledMode == 1) {
    // Brighten color mode colors on mode change to show the user which mode it is.
    if (isColorModeChanged) {
      clearLeds();

      for (int led = 0; led < 3; led++) {
        for (int color = 0; color < 3; color++) {
          ledPwms[led][color] = PWM_MAX;
        }
      }
    }

    int speedMod = calcExp(ledSpeedMod, SPEED_MOD_MIN, SPEED_MOD_MAX, 1.5);
    for (int led = 0; led < 3; led++) {
      for (int color = 0; color < 3; color++) {
        int pwm = setLedFadePwm(led, color, speedMod);

        int ledDriverIndex = led * 3 + color;
        if (!COLOR_MODES[colorMode][ledDriverIndex]) {
          continue;
        }

        if (colorScope == 0) {
          pwmDriver.setPWM(ledDriverIndex, 0, pwm);
        } else if (colorScope == 1) {
          // All colors of led same pwm as first color.
          pwmDriver.setPWM(ledDriverIndex, 0, ledPwms[led][0]);
        }
      }
    }
  } else if (ledMode == 2) {
    float speedMod = SPEED_MOD_MAX + SPEED_MOD_MIN - ledSpeedMod;
    speedMod = calcExp(speedMod, SPEED_MOD_MIN, SPEED_MOD_MAX);
    int timeBetweenColorChange = map(speedMod, SPEED_MOD_MIN, SPEED_MOD_MAX, LED_TOGGLE_TIME_MIN, LED_TOGGLE_TIME_MAX);
    if (millis() - lastColorChange >= timeBetweenColorChange) {
      lastColorChange = millis();

      bool colorCombination[9] = {};
      do {
        for (int color = 0; color < 9; color++) {
          if (random(2) == 1) {
            colorCombination[color] = true;
          } else {
            colorCombination[color] = false;
          }
        }

        // Prevent darkness
        colorCombination[random(9)] = true;
      } while (compareColorCombinations(colorCombination, lastColorCombination));

      clearLeds();
      for (int color = 0; color < 9; color++) {
        if (colorCombination[color]) {
          pwmDriver.setPWM(color, 0, PWM_MAX);
        }
      }

      for (int color = 0; color < 9; color++) {
        lastColorCombination[color] = colorCombination[color];
      }
    }
  }
}

float calcExp(float value, float min, float max) {
  return calcExp(value, min, max, 2.0);
}

float calcExp(float value, float min, float max, float curve) {
  float norm = (value - min) / (max - min);
  norm = constrain(norm, 0.0, 1.0);
  float curved = pow(norm, curve);
  return min + curved * (max - min);
}

int setLedFadePwm(int led, int color, float speedMod) {
  float pwmChangeAmount = LED_BASE_STEPS * ledSpeeds[led][color] * (speedMod / 10) * ledDirections[led][color];
  // Fade speed depth modifier if motor is in depth mode.
  if (motorMode == 2) {
    pwmChangeAmount *= LED_FADE_DEPTH_SPEEDS[led];
  }

  int pwm = ledPwms[led][color] + pwmChangeAmount;
  if (pwm > PWM_MAX) {
    ledDirections[led][color] = -1;
    pwm = PWM_MAX;
  } else if (pwm < LED_MIN_PWM) {
    ledDirections[led][color] = 1;
    pwm = LED_MIN_PWM;
  }

  ledPwms[led][color] = pwm;

  if (millis() - ledSpeedChangeTimes[led][color] >= ledSpeedTimesBeforeChange[led][color]) {
    ledSpeedChangeTimes[led][color] = millis();
    ledSpeedTimesBeforeChange[led][color] = random(LED_SPEED_CHANGE_TIME_MIN, LED_SPEED_CHANGE_TIME_MAX+1);
    ledSpeeds[led][color] = randomFloat(LED_SPEED_MIN, LED_SPEED_MAX);
  }

  return pwm;
}

bool compareColorCombinations(bool* combination1, bool* combination2) {
  if (combination1 == nullptr || combination2 == nullptr) {
    return combination1 == nullptr && combination2 == nullptr;
  }

  bool isIdentical = true;
  for (int color = 0; color < 9; color++) {
    if (combination1[color] != combination2[color]) {
      isIdentical = false;
      break;
    }
  }

  return isIdentical;
}

void loopMotors() {
  if (motorMode == 0) {
    clearMotors();
  } else {
    for (int motor = 0; motor < 3; motor++) {
      float speedMod = map(motorSpeedMod, SPEED_MOD_MIN, SPEED_MOD_MAX, MOTOR_MIN_PWM, PWM_MAX);
      if (motorMode == 2) {
        speedMod *= MOTOR_DEPTH_SPEEDS[motor];
      }

      int pwm = calcExp(speedMod, MOTOR_MIN_PWM, PWM_MAX, 2.5);
      pwmDriver.setPWM(motor + 9, 0, pwm);
    }
  }
}
